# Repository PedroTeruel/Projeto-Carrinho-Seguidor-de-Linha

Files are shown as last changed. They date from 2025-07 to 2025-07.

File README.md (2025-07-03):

# Como Construir um Carrinho Seguidor de Linha: Guia Passo a Passo

## Introdução

Como um dos projetos mais clássicos para introdução a engenharia, a construção de um carrinho seguidor de linha: um robô autônomo capaz de detectar e seguir uma trilha no chão, permite aplicar conhecimentos teóricos de forma pratica, estimulando raciocínio logico e solução de problemas.

Este artigo apresenta um passo a passo completo para criar um projeto funcional de carrinho seguidor de linha, desde a construção do circuito eletrônico até a montagem mecânica do robô. O projeto foi construído por mim no 1º semestre da engenharia de computação do Senac São Paulo e aborda conhecimentos de eletrônica, soldagem, modelagem 3D, lógica de sensores e controle de motores.

O principal objetivo foi a construção de um carrinho seguidor de linha que funciona como um robô autônomo capaz de identificar e seguir uma trilha contínua através de sensores infravermelhos, interpretando os dados em tempo real para corrigir sua trajetória e manter o movimento sobre a trilha.

Veja nos vídeos dos links abaixo o funcionamento do carrinho que você irá aprender a construir nesse artigo:
- 🔗 [Vídeo 1 – Funcionamento do Carrinho](https://www.youtube.com/watch?v=o5KDZBv2Lis)
- 🔗 [Vídeo 2 – Detalhes do Circuito](https://www.youtube.com/shorts/yLg4nNAEKBg)

## Materiais Necessários
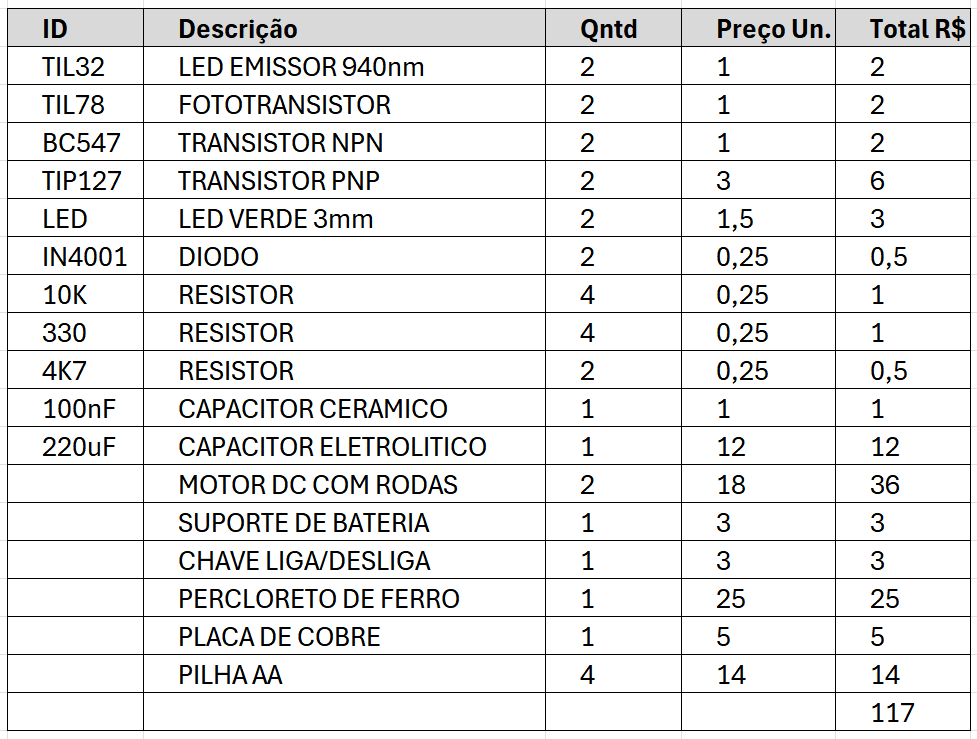
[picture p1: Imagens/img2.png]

## Circuito lógico
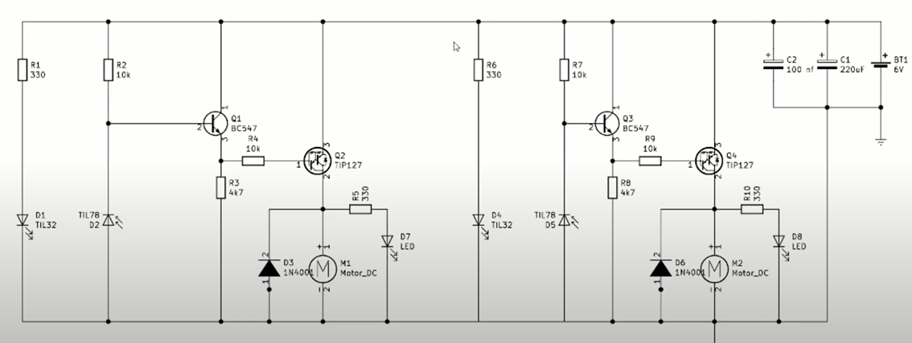
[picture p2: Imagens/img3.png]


O circuito é composto por dois blocos simétricos, um para o controle do motor esquerdo e outro para o direito. Cada bloco utiliza um LED emissor infravermelho (D1/D4 – TIL32) e um fototransistor (D2/D5 – TIL78) para detectar a linha preta sobre o chão. O LED emite luz infravermelha constantemente, e o fototransistor detecta a luz refletida: superfícies claras refletem mais luz, e superfícies escuras (como a linha preta) refletem menos.

Quando o sensor (D2/D5) recebe a luz refletida, ele conduz corrente para a base do transistor NPN Q1/Q3 (BC547) por meio do resistor R2/R7 (10kΩ). Isso faz com que o transistor (Q1/Q3) conduza, permitindo que sua saída vá para o GND. Essa saída está conectada à base do segundo transistor, um PNP TIP127 (Q2/Q4), por meio de R3/R8 (4k7Ω). Quando a base do TIP127 é puxada para o GND, ele conduz, ligando o motor M1/M2 e acendendo o LED indicador D7/D8, indicando que o motor está em funcionamento.

O resistor R1/R6 (330Ω) está em série com o LED emissor (D1/D4) para limitar a corrente, enquanto R5/R10 (330Ω) protege os LEDs indicadores (D7/D8). Os diodos D3/D6 (1N4001) são colocados em paralelo com os motores para proteger o circuito de picos de tensão.

Por fim, os capacitores C1 (220µF) e C2 (100nF), ligados à alimentação vinda da bateria de 6V (BT1), são usados para estabilizar a tensão, filtrando ruídos e evitando oscilações no funcionamento do circuito. 

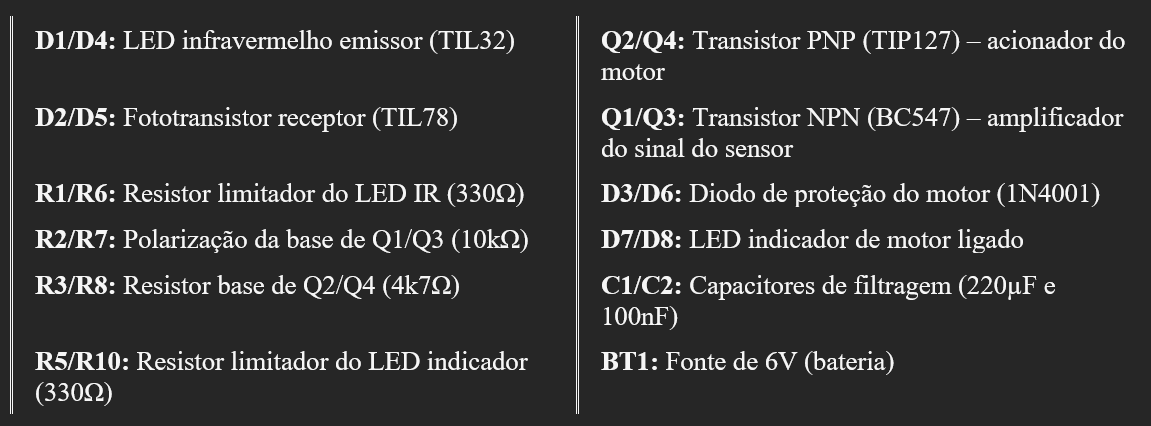
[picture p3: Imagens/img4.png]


Esse circuito, gerará a placa abaixo, que será construída no decorrer desse projeto.

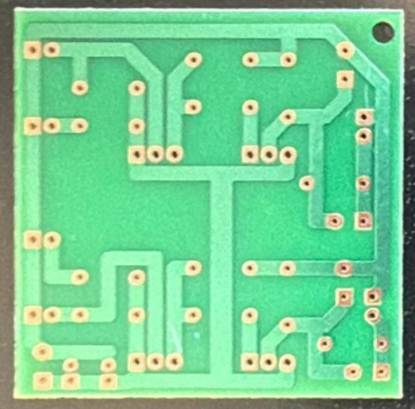
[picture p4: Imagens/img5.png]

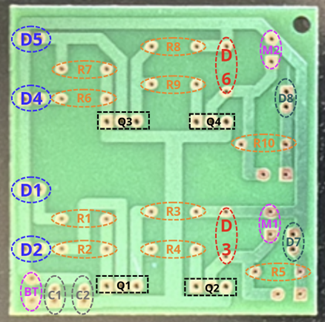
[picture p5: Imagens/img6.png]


Convenção comum em PCBs: 
  Ilha quadrada → Positivo (+) 
  Ilha circular → Negativo (–)

## Etapas do Projeto
###   1. Desenvolvimento da placa de circuito
1- Na placa de cobre, desenhe as trilhas com base no circuito logico utilizando um lápis para esboço, depois passe a caneta permanente. Lembre-se de desenhar as ilhas de solda grandes o suficiente para os furos dos componentes.

2- Corte a placa no tamanho adequado e realizamos os furos para as ilhas de solda.

3- Mergulhe a placa no percloreto de ferro por 30 minutos, até que o cobre excedente seja corroído.

4- Após a corrosão, lave a placa com água para remover o excesso de percloreto, limpe a tinta da caneta com álcool e utilize borracha para finalizar a limpeza.

Obs: Descarte o percloreto usado em local apropriado. Nunca jogue na pia.

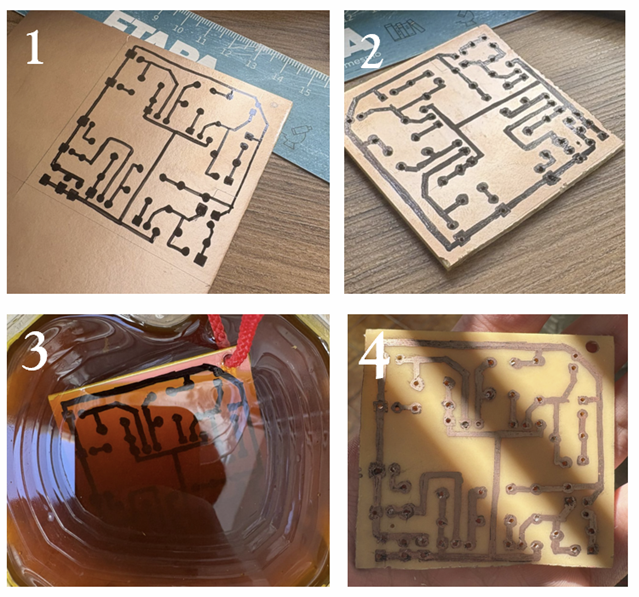
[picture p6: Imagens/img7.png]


### 2. Perfuração e Soldagem dos Componentes

Fure a placa nos pontos adequados usando uma furadeira ou ferramenta manual e solde os componentes na seguinte ordem:

1- Resistores e capacitores (R1-R10 e C1-C2)

2- Diodos e transistores (D3, D6 e Q1-Q4)

3- Sensores TIL32 e TIL78 (D1, D2 e D4, D5) (**Obs: Os Sensores devem ser soldados no lado das trilhas da placa, pois eles que identificarão a linha a ser seguida) (Não solde os sensores colados na 4- plaquinha, deixe uma sobra na perna para ajustes futuros**)4

5- LEDs (D7-D8)

6- Motores e suporte de pilhas (BT1, M1 e M2)

7- **Os fios são ligados da seguinte maneira: Os fios que saem de M1 da placa ligam direto no motor, e o mesmo vale para M2. Para BT1, o fio que sai do positivo liga no interruptor, e o fio que sai do negativo liga direto na bateria. Para finalizar, o positivo da bateria liga no outro ponto do interruptor.**

Obs: Certifique-se de que os motores estejam girando para o lado certo (com as ligações apontando para dentro).

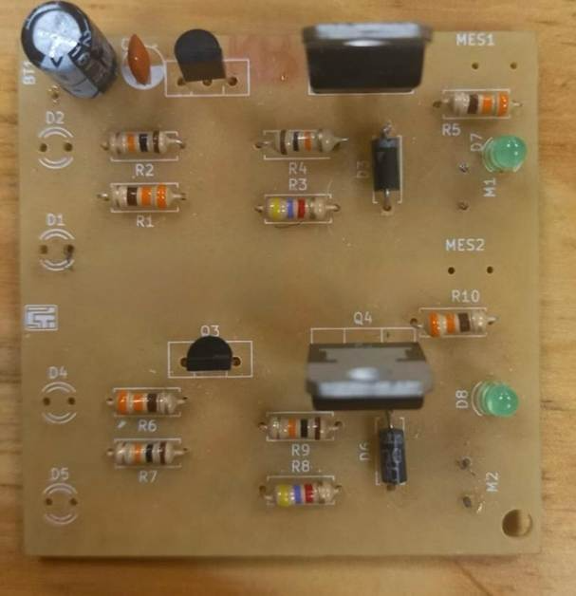
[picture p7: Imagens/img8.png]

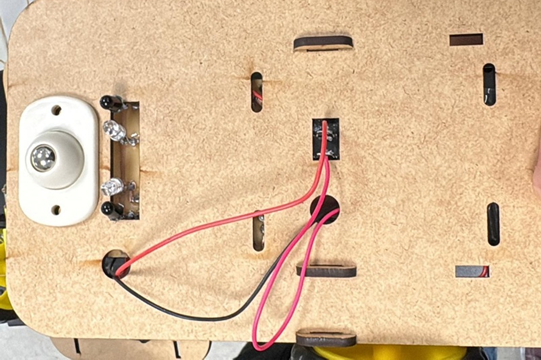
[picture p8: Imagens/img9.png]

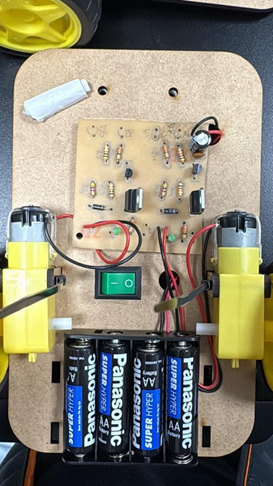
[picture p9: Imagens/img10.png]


### 3. Construção do Chassi

O chassi do carrinho foi construído com base no modelo 3D utilizando o SolidWorks. Em uma placa de MDF, foi cortado e furado a laser para maior precisão, porém, é possível construí-lo manualmente ou utilizando uma impressora 3D.

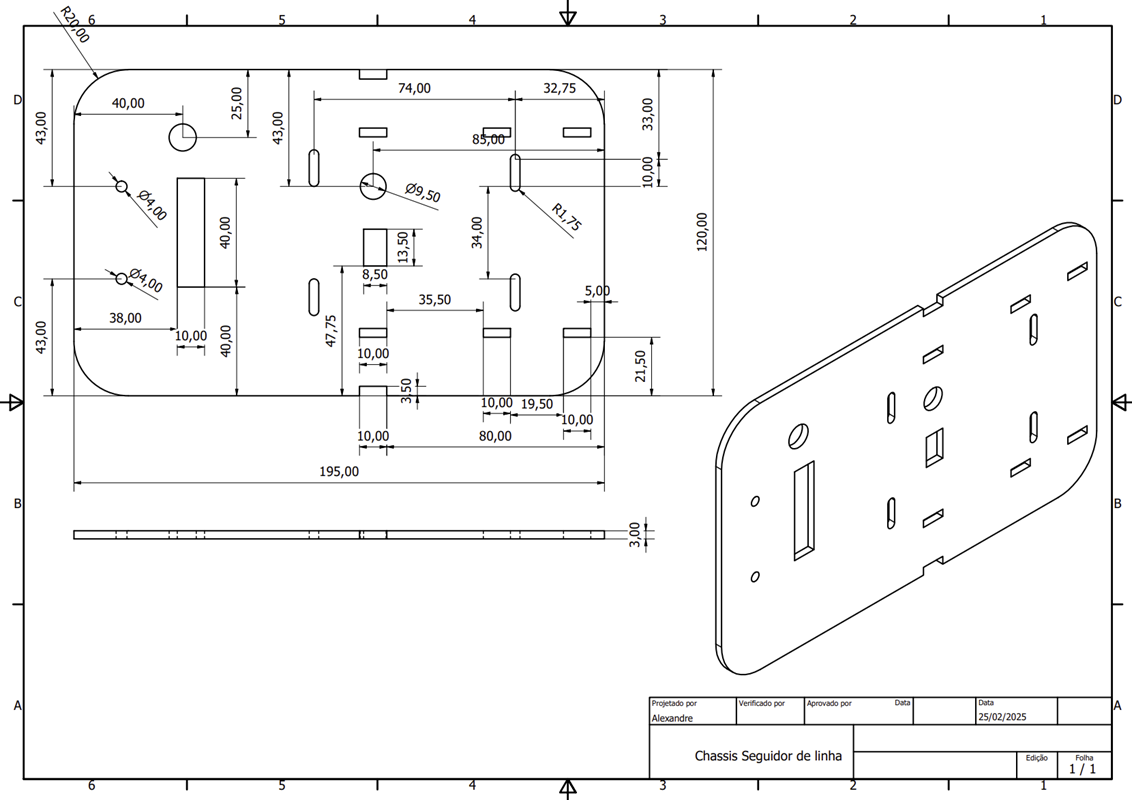
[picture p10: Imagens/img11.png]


### 4. Montagem

-Fixe os motores DC com rodas nas laterais do chassi, deixando espaço entre eles para a placa de circuito.

-Na parte inferior dianteira, coloque o circuito, com os sensores infravermelhos voltados para o chão.

-Conecte o suporte de pilhas e a chave liga/desliga de forma acessível.

-Prenda tudo com parafusos ou cola quente, conforme o material do chassi.

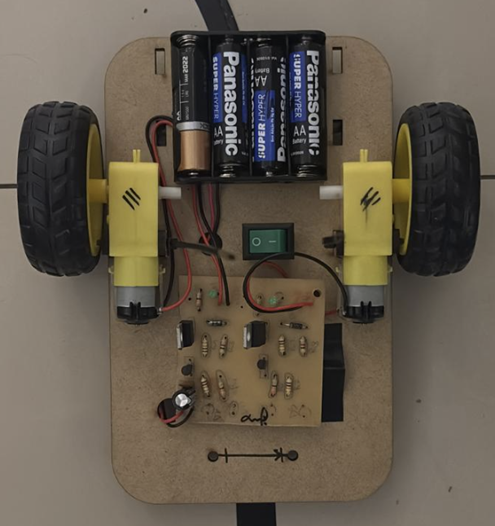
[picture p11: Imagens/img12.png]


## Funcionamento e lógica de controle

O carrinho funciona de maneira autônoma, sem a necessidade de um microcontrolador simulando aplicações reais da automação. No circuito, o LED infravermelho emite sinal constantemente, enquanto o fototransistor detecta a reflexão da superfície. Quando o carrinho passa por uma linha preta, o fototransistor não recebe o sinal pois ele não é refletido de volta, assim, essa variação de sinal controla os transistores que ligam ou desligam os motores.

-Se o sensor esquerdo não recebe o sinal → motor esquerdo é desativado → o carrinho vira para a esquerda.

-Se o sensor direito não recebe o sinal→ motor direito é ativado → o carrinho vira para a direita.

-Se ambos detectam branco → ambos os motores funcionam → o carrinho segue reto.

## Testes e ajustes

Os ajustes são essenciais para o bom funcionamento do carrinho, principalmente nos sensores.   Caso o carrinho não esteja detectando uma curva, é necessário regular a altura dos sensores para melhor leitura. Além disso, os sensores devem estar em “V” para que o sinal retorne para o receptor, dessa forma é preciso regular até achar a posição ideal dos sensores.

Caso o carrinho esteja muito rápido, é necessário ajustar a velocidade para que o carrinho passe mais devagar na curva e os sensores possam detectar e desligar o motor a tempo. A velocidade pode ser reduzida utilizando pilhas menos carregadas, alterando as resistências, ou retirando uma das pilhas e fechando o circuito da caixa de bateria.

## Pontos de Atenção Observados

-Em curvas muito fechadas, o carrinho tem dificuldade de se manter na linha, devido ao espaçamento entre os sensores.

-É necessário ajustar a altura dos sensores para melhorar a sensibilidade na detecção da linha.

-A potência dos motores tem impacto direto na estabilidade: velocidades mais altas dificultaram o controle do carrinho.

## Conclusão

A construção do carrinho seguidor de linha é uma boa introdução à engenharia e automação. Com esse projeto é possível aprender conceitos fundamentais como sensores, transistores, controle de motores e montagem de circuitos. Além disso, estimula habilidades manuais e de resolução de problemas. Esse artigo mostra que, com dedicação, mesmo utilizando materiais simples e de baixo custo, é possível desenvolver um robô funcional, que exemplifica de forma clara o funcionamento de sistemas autônomos no mundo real.

## LinkedIn

Você pode acessar informações sobre esse projeto no meu linkedin clicando nesse link 

- [Como Construir um Carrinho Seguidor de Linha – Guia Passo a Passo (LinkedIn)](https://www.linkedin.com/pulse/como-construir-um-carrinho-seguidor-de-linha-guia-passo-teruel-rvckc)

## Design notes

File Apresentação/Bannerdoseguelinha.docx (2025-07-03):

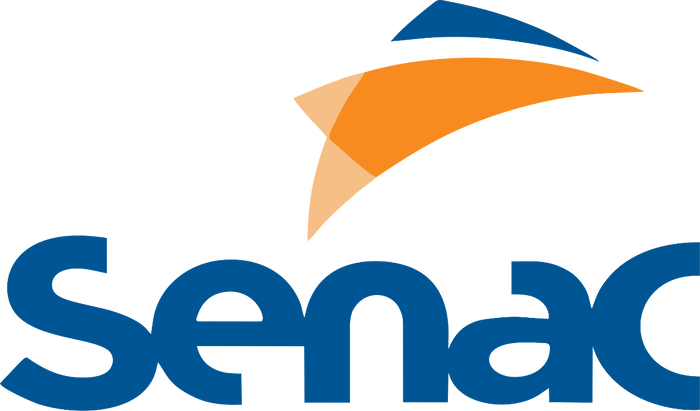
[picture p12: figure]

# RESUMO

12ª Semana das Engenharias do Senac

Centro Universitário Senac - Campus Santo Amaro - Senac SP 02 de junho e 07 de junho de 2025

# CARRINHO SEGUIDOR DE LINHA ANALÓGICO

Grupo: Iniciativa Proativa

# RESULTADOS E DISCUSSÃO

O projeto desenvolveu um carrinho autônomo seguidor de linha, integrando conhecimentos do 1º semestre do curso. Utilizando sensores ópticos, o sistema detecta variações de luminosidade entre superfícies claras e escuras e ajusta os motores em tempo real para manter a trajetória definida.

PALAVRAS-CHAVE: Aprendizagem baseada em projetos, eletrônica analógica, modelagem 3D, seguidor de linha, robótica.

# INTRODUÇÃO

Nosso projeto busca explorar a interseção entre a robótica e a automação, criando um sistema autônomo capaz de seguir uma linha sobre uma superfície. O carrinho foi desenvolvido como parte das atividades práticas interdisciplinares, integrando os conhecimentos adquiridos no 1º semestre do curso. O funcionamento do carrinho se baseia na detecção da diferença de intensidade luminosa entre superfícies claras e escuras. Sensores ópticos detectam essa variação e enviam sinais ao circuito de controle, que ajusta o comportamento dos motores em tempo real, garantindo que o carrinho siga a trajetória estabelecida.

# METODOLOGIA

# Após a intodução das primeiras aulas, o grupo fez uma análise dos componentes necessários, iniciou-se a fase prática com os seguintes passos:

1. Organização dos Materiais: Separação e teste dos sensores, motores, resistores, transistores, LEDs e fios. 2. Montagem do Chassi: Desenvolvemos no SolidWorks com base no modelo adequado ao encaixe dos motores e sensores, e depois levamos a uma estrutura de furação a laser. 3. Instalação dos Sensores e Motores: O sensor foi posicionado na parte inferior da frente do carrinho, garantindo rápida resposta aos desvios de trajetória. E os moteres ao lado da placa, para gerar uma estabilidade para o carrinho 4. Soldagem da Placa de Circuito: Fizemos a montagem de um circuito funcional com resistores, transistores e LEDs, conectando-os aos motores 5. Conexão da Fonte de Alimentação: Conectamos a bateria de 6V com instalação de uma microchave para acionamento. 6. Testes e Ajustes Finais: Ajustamos os sensores na melhor posição para garantir melhor sensibilidade e resposta precisa do carrinho.

O carrinho foi capaz de seguir com precisão a linha preta sobre superfície branca. demostrando eficiencia, corrigindo automaticamente a trajetória em caso de desvios, com desempenho estável fazendo curvas suaves. Alguns destaques foi a resposta rápida a mudanças de direção, e ajustes na altura dos sensores e na velocidade dos motores foram fundamentais para otimizar a performance. O projeto proporcionou uma vivência prática valiosa, reforçando conceitos de automação, eletrônica analógica e trabalho em equipe.

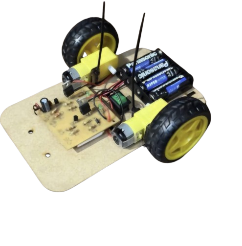
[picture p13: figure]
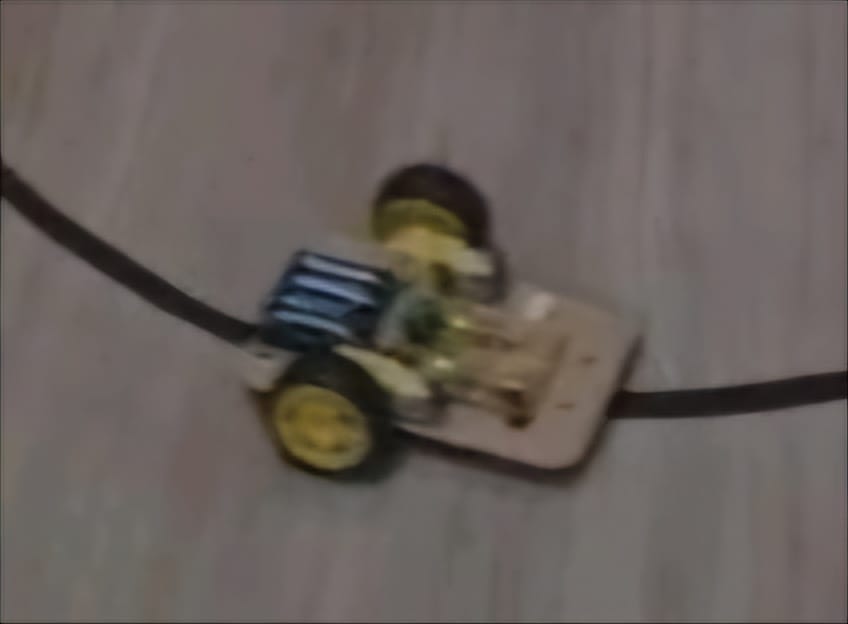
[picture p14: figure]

Figura 1. Imagem do carrinho

Figura 2. Imagem do carrinho seguindo a linha

# CONCLUSÃO

O desenvolvimento do carrinho seguidor de linha foi um exercício fundamental para aplicar os conhecimentos adquiridos nas disciplinas do semestre, com ênfase especial na eletrônica, que foi essencial para a montagem do circuito e o funcionamento do sistema. O projeto permitiu vivenciar a complexidade de transformar uma ideia em um projeto funcional, promovendo aprendizado técnico e colaborativo, incluindo a montagem e soldagem de circuitos eletrônicos, a aplicação prática de sensores, transistores e motores, trabalho em equipe e resolução de problemas técnicos, com uma gestão de qualidade, desde de o planejamento até os testes finais.

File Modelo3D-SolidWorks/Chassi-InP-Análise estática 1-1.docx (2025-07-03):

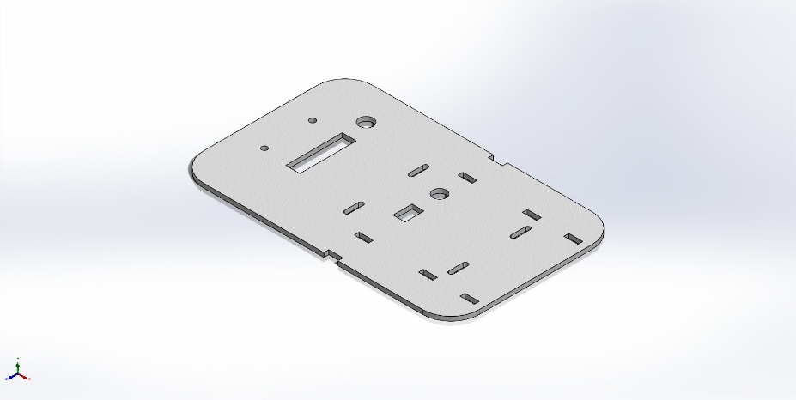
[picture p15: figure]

Simulação de Chassi-InP

Data: sábado, 12 de abril de 2025
Projetista: Pedro Teruel

Nome do estudo: Análise estática 1

Tipo de análise: Análise estática
Descrição Sem dados

# Pressuposições

# Informações do modelo

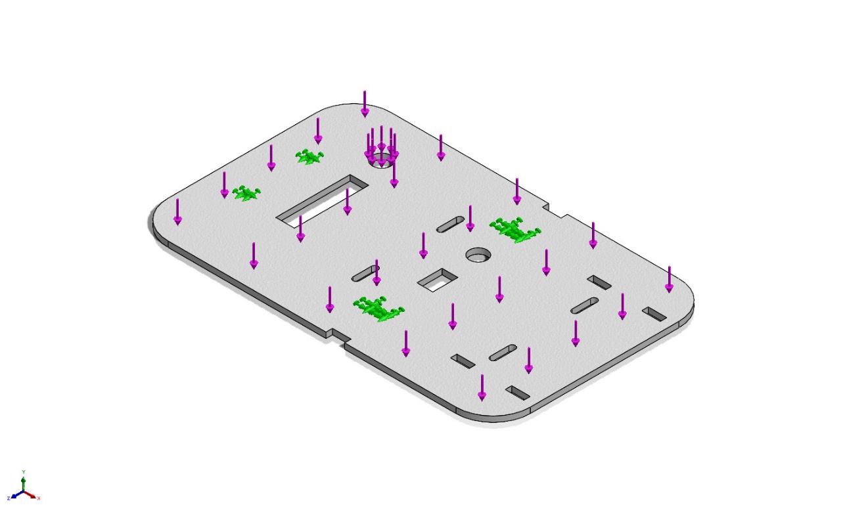
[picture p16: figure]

Nome do modelo: Chassi-InP

Configuração atual: Valor predeterminado

Corpos sólidos
Nome e referência do documento | Tratado como | Propriedades volumétricas | Caminho/Data do documento modificado

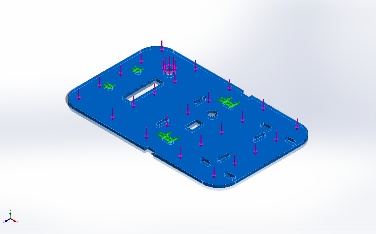
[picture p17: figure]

Corte-extrusão4 | Corpo sólido | Massa:0,0782146 kg Volume:6,57265e-05 m^3 Densidade:1.190 kg/m^3 Peso:0,766503 N | D:\SENAC\ProjInt\Chassi-InP.SLDPRT Mar 29 08:10:08 2025

# Propriedades do estudo

Nome do estudo | Análise estática 1
Tipo de análise | Análise estática
Tipo de malha | Malha sólida
Efeito térmico: | Ativada
Opção térmica | Incluir cargas de temperatura
Temperatura de deformação zero | 298 Kelvin
Inclui efeitos da pressão de fluidos do SOLIDWORKS Flow Simulation | Desativada
Tipo de Solver | Automático
Efeito no plano: | Desativada
Mola suave: | Desativada
Atenuação inercial: | Desativada
Opções de união incompatíveis | Automático
Grande deslocamento | Desativada
Calcular forças de corpo livre | Ativada
Atrito | Desativada
Usar método adaptável: | Desativada
Pasta de resultados | Documento do SOLIDWORKS (D:\SENAC\ProjInt)

# Unidades

Sistema de unidades: | SI (MKS)
Comprimento/Deslocamento | mm
Temperatura | Kelvin
Velocidade angular | Rad/s
Pressão/Tensão | N/m^2

# Propriedades do material

Referência do modelo | Propriedades | Componentes

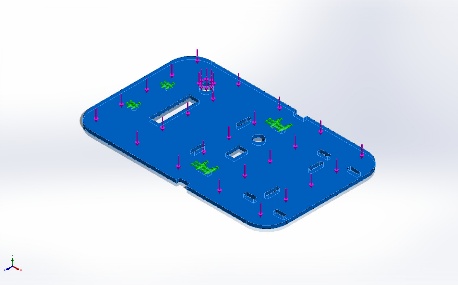
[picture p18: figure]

| Nome: PMMA Tipo de modelo: Isotrópico linear elástico Critério de falha predeterminado: Desconhecido Resistência à tração: 6,1e+07 N/m^2 Resistência à compressão: 1,05e+08 N/m^2 Módulo elástico: 2,77e+09 N/m^2 Massa específica: 1.190 kg/m^3 | Corpo sólido 1(Corte-extrusão4)(Chassi-InP)

Dados da curva:N/A

# Acessórios de fixação e Cargas

Nome do acessório de fixação | Imagem de acessório de fixação | Detalhes de acessório de fixação

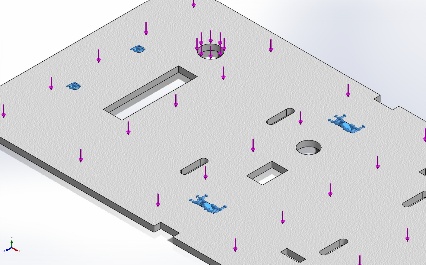
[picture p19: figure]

Fixo-1 | | Entidades: 10 face(s) Tipo: Geometria fixa

Forças resultantes

Componentes | X | Y | Z | Resultante
Força de reação(N) | -3,02494e-06 | 30 | -8,19564e-08 | 30
Momento de reação(N.m) | 0 | 0 | 0 | 0

Nome da carga | Carregar imagem | Detalhes de carga

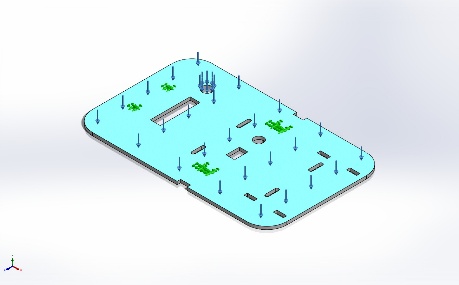
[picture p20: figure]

Força-1 | | Entidades: 1 face(s) Tipo: Aplicar força normal Valor: 30 N

# Definições de conector

Sem dados

# Informações de interação

Sem dados

# Informações de malha

Tipo de malha | Malha sólida
Gerador de malhas usado: | Malha mesclada com base em curvatura
Pontos Jacobianos para malha de alta qualidade | 16 Pontos
Tamanho máximo de elemento | 6 mm
Tamanho de elemento mínimo | 1 mm
Qualidade da malha | Alta

## Informações de malha - Detalhes

Total de nós | 14661
Total de elementos | 7220
Proporção máxima | 6,8121
% de elementos com Proporção < 3 | 98
Porcentagem de elementos com Proporção > 10 | 0
Porcentagem de elementos distorcidos | 0
Tempo para conclusão da malha (hh;mm;ss): | 00:00:03
Nome do computador:

## Plotagens de qualidade de malha

Nome | Tipo | Mín. | Máx.
Qualidade1 | Malha | - | -

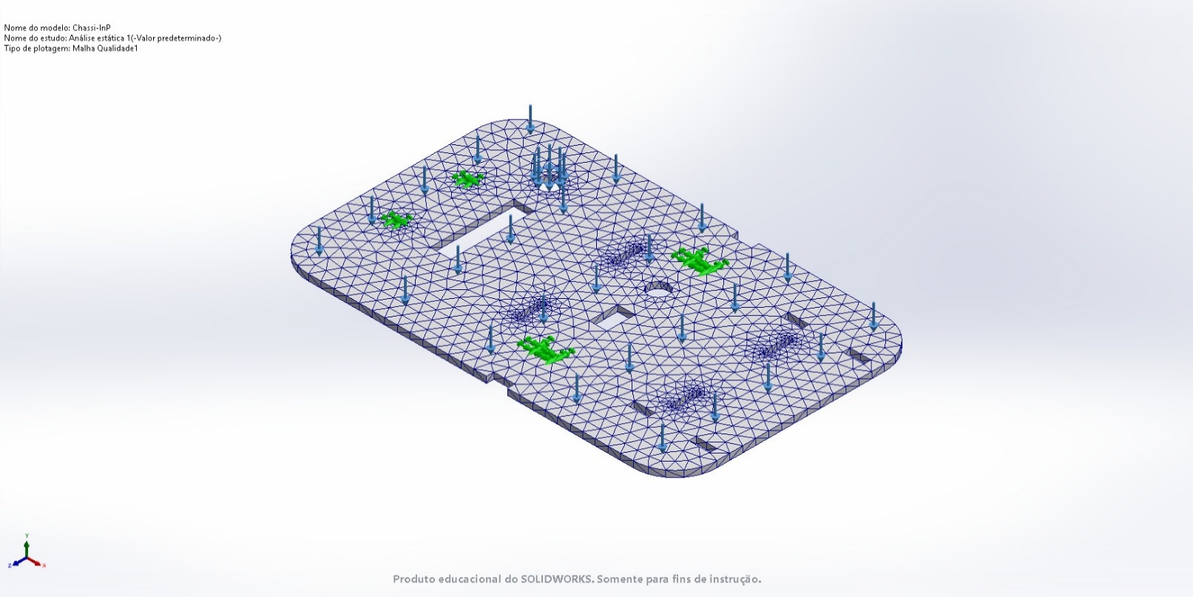
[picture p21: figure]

Chassi-InP-Análise estática 1-Qualidade-Qualidade1

# Detalhes do sensor

Sem dados

# Forças resultantes

## Forças de reação

Conjunto de seleção | Unidades | Soma X | Soma Y | Soma Z | Resultante
Modelo inteiro | N | -3,02494e-06 | 30 | -8,19564e-08 | 30

## Momentos de reação

Conjunto de seleção | Unidades | Soma X | Soma Y | Soma Z | Resultante
Modelo inteiro | N.m | 0 | 0 | 0 | 0

## Forças de corpo livre

Conjunto de seleção | Unidades | Soma X | Soma Y | Soma Z | Resultante
Modelo inteiro | N | -6,88434e-06 | -4,2174e-05 | -5,28991e-07 | 4,27355e-05

## Momentos de corpo livre

Conjunto de seleção | Unidades | Soma X | Soma Y | Soma Z | Resultante
Modelo inteiro | N.m | 0 | 0 | 0 | 1e-33

# Vigas

Sem dados

# Resultados do estudo

Nome | Tipo | Mín. | Máx.
Tensão1 | VON: tensão de von Mises | 1,553e+03N/m^2 Nó: 11834 | 7,048e+06N/m^2 Nó: 14470

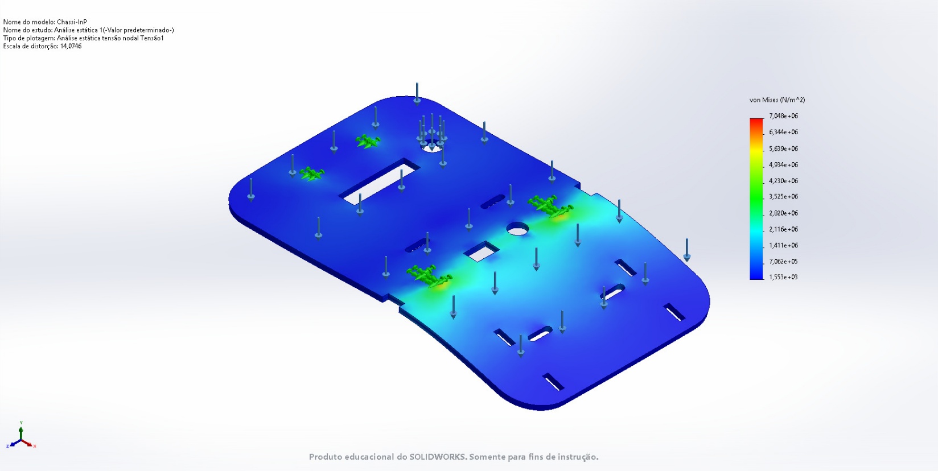
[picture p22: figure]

Chassi-InP-Análise estática 1-Tensão-Tensão1

Nome | Tipo | Mín. | Máx.
Deslocamento1 | URES: Deslocamento resultante | 0,000e+00mm Nó: 27 | 1,386e+00mm Nó: 8977

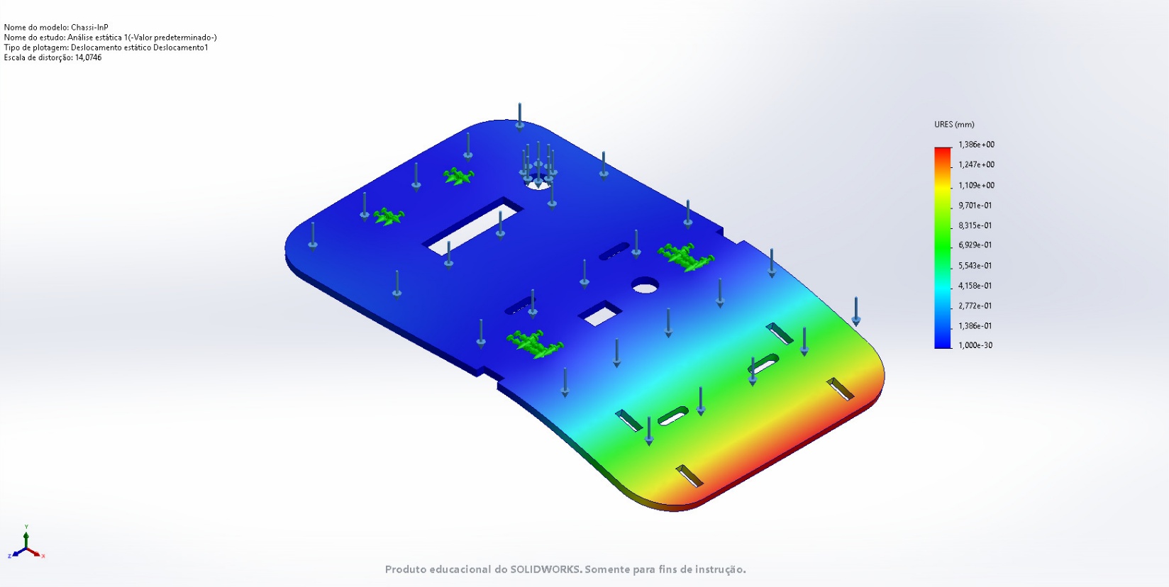
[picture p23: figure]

Chassi-InP-Análise estática 1-Deslocamento-Deslocamento1

Nome | Tipo | Mín. | Máx.
Deformação1 | ESTRN : Deformação equivalente | 1,068e-07 Elemento: 3222 | 7,474e-04 Elemento: 6243

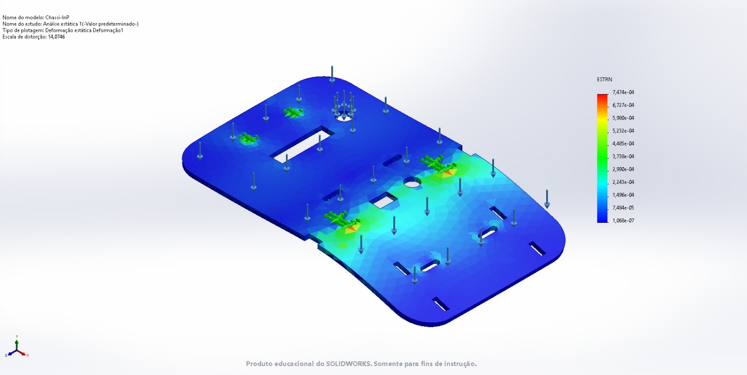
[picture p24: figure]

Chassi-InP-Análise estática 1-Deformação-Deformação1

Nome | Tipo
Deslocamento1{1} | Forma deformada

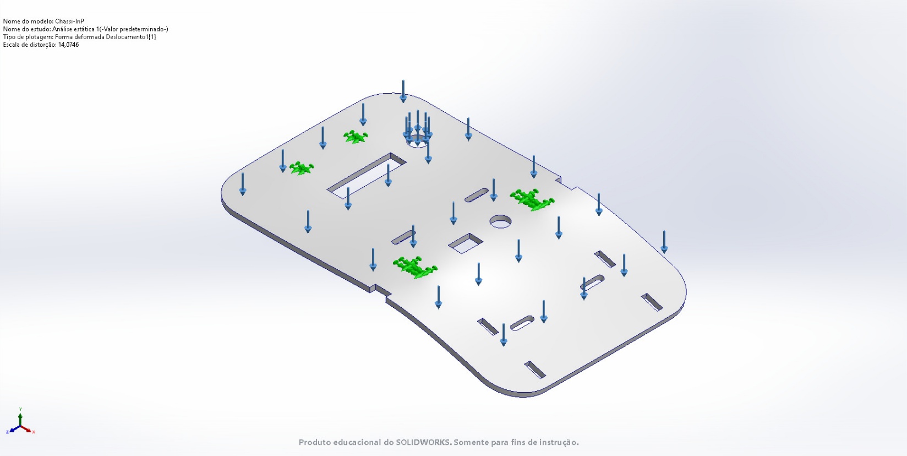
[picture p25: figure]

Chassi-InP-Análise estática 1-Deslocamento-Deslocamento1{1}

# Conclusão

Analisado com o SOLIDWORKS Simulation Simulação de Chassi-InP 16

Analisado com o SOLIDWORKS Simulation Simulação de Chassi-InP 1

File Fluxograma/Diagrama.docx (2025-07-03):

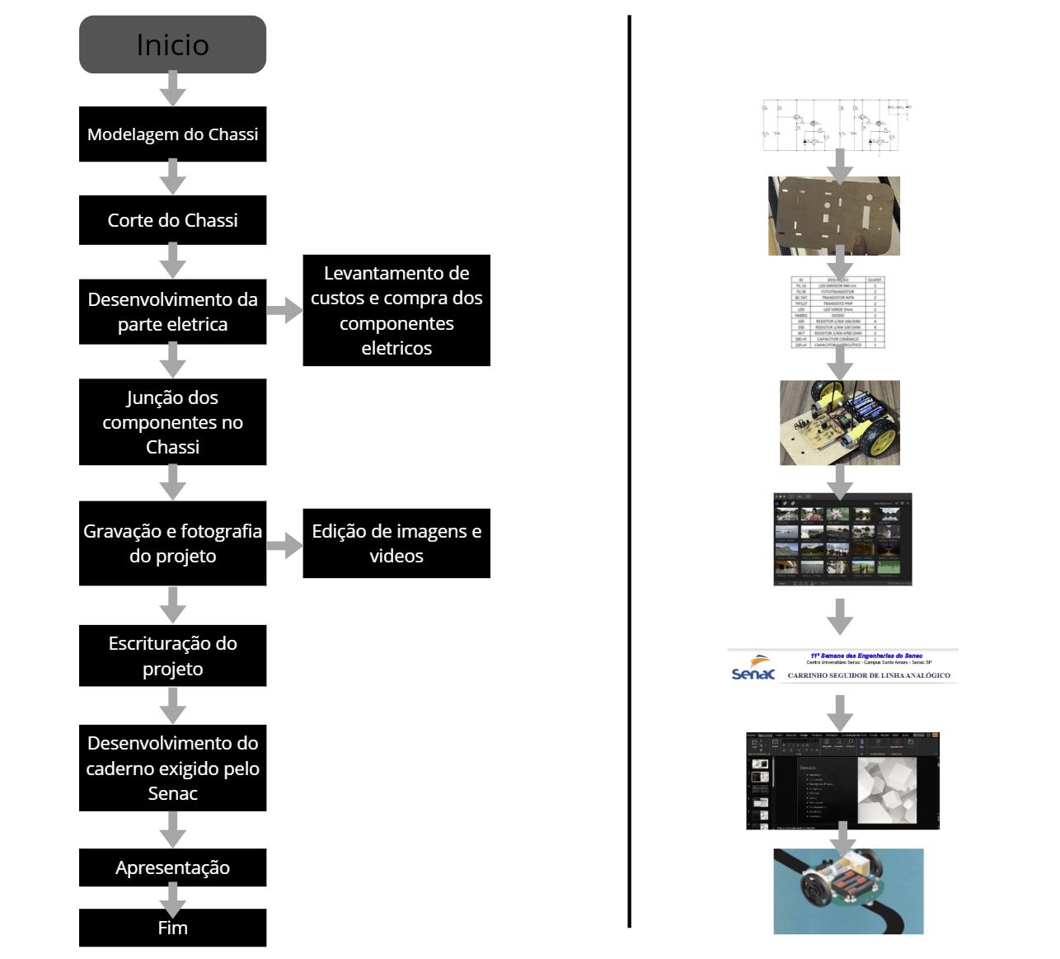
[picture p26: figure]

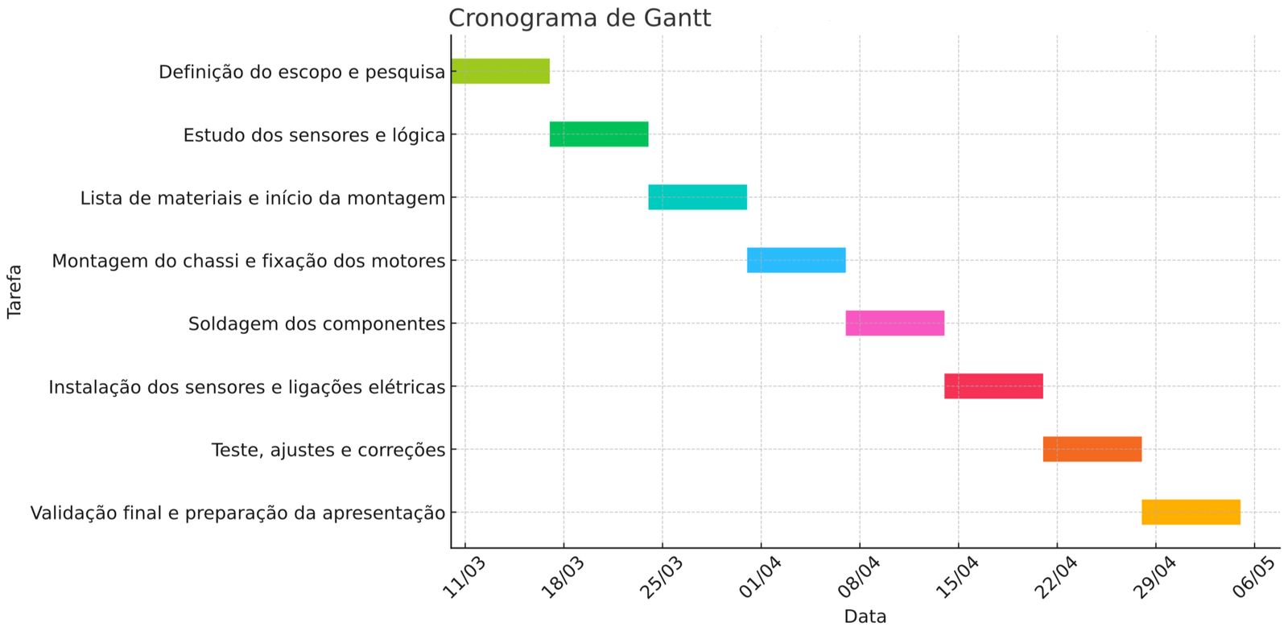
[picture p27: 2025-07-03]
Gantt.jpeg

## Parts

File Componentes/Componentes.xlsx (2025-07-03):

ID | Descrição | Qntd | Preço Un. | Total R$
TIL32 | LED EMISSOR 940nm | 2 | 1 | 2
TIL78 | FOTOTRANSISTOR | 2 | 1 | 2
BC547 | TRANSISTOR NPN | 2 | 1 | 2
TIP127 | TRANSISTOR PNP | 2 | 3 | 6
LED | LED VERDE 3mm | 2 | 1.5 | 3
IN4001 | DIODO | 2 | 0.25 | 0.5
10K | RESISTOR | 4 | 0.25 | 1
330 | RESISTOR | 4 | 0.25 | 1
4K7 | RESISTOR | 2 | 0.25 | 0.5
100nF | CAPACITOR CERAMICO | 1 | 1 | 1
220uF | CAPACITOR ELETROLITICO | 1 | 12 | 12
 | MOTOR DC COM RODAS | 2 | 18 | 36
 | SUPORTE DE BATERIA | 1 | 3 | 3
 | CHAVE LIGA/DESLIGA | 1 | 3 | 3
 | PERCLORETO DE FERRO | 1 | 25 | 25
 | PLACA DE COBRE | 1 | 5 | 5
 | PILHA AA | 4 | 14 | 14
 |  |  |  | 117

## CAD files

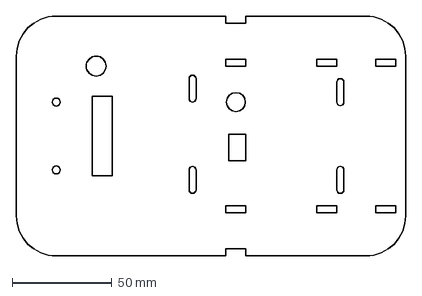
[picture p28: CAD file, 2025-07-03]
Modelo3D-SolidWorks/Chassi-InP.DXF
195.0 x 120.0 mm

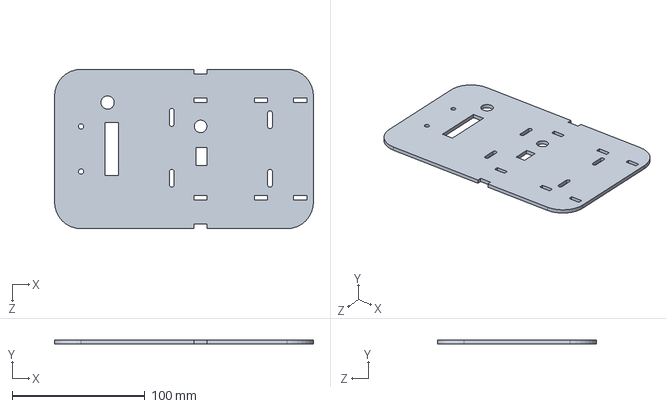
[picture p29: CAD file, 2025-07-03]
Modelo3D-SolidWorks/Chassi.SLDPRT
195.0 x 3.00 x 120.0 mm
